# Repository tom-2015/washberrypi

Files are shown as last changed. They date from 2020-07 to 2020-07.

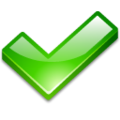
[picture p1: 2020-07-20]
www/ok.png

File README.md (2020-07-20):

# WashberryPi
The main controller board of our washing machine was broken so I decided to do something stupid: create a new controller board with a Raspberry Pi on it!
It turned out not so easy as thought, especially starting centrifuge without having unbalance making the machine to start walking proved a challenge.
After a few months testing and designing new PCB it was finally working again. It's not yet fully completed but if anyone else ever wants to do something this crazy I decided to put everything open source on github.

# Requirements
It's designed for a Samsung co bubble with DC motor but with some adjustments in software and PCB it will probably work with other machines that have a DC motor.
You'll need some skills for PCB design in Eagle, programming Raspberry Pi (Visual Basic .NET) and microcontrollers (Microchip PIC) in C.

# Contens
The repository contains 4 projects:
* Washmachine.sln: the main Visual Studio VB .NET project with software that runs on the Raspberry. This project is the main program of the washing machine. It controls all the components and provides a web interface.
* eagle directory: contains the Eagle files and Gerber files for the PCB that holds the Raspberry Pi Zero W, PIC microcontroller, relays and motor control components.
* pic directory: contains washing_machine.__c which is a Source Boost project containing C-code for the microcontroller that drives the TRIAC for motor.
* www directory: this is the web interface main directory.

# TIPS
Some tips if you want to make your washing machine Raspberry Pi controlled:
* be careful when applying power to the motor, I accidently applied power too fast resulting in a broken bearing! When testing the motor circuit add some resistors in series with the motor.
* If I need to redo the project I would consider using PWM with an IGBT or MOSFET to drive the motor and not using the original Samsung design with a TRIAC. This is because I think it's easier using PWM which in theory could be connected directly to the Pi instead of having a different microcontroller for it.
* Use a Raspberry Pi (2,3,4) with quad core instead of the single core Raspberry Pi Zero W. I needed to use an accelerometer to capture the drum vibrations and this required a thread to read 400 samples a second over I²C. This single core is often interrupted doing other stuff making the accelerometer buffer overflow.

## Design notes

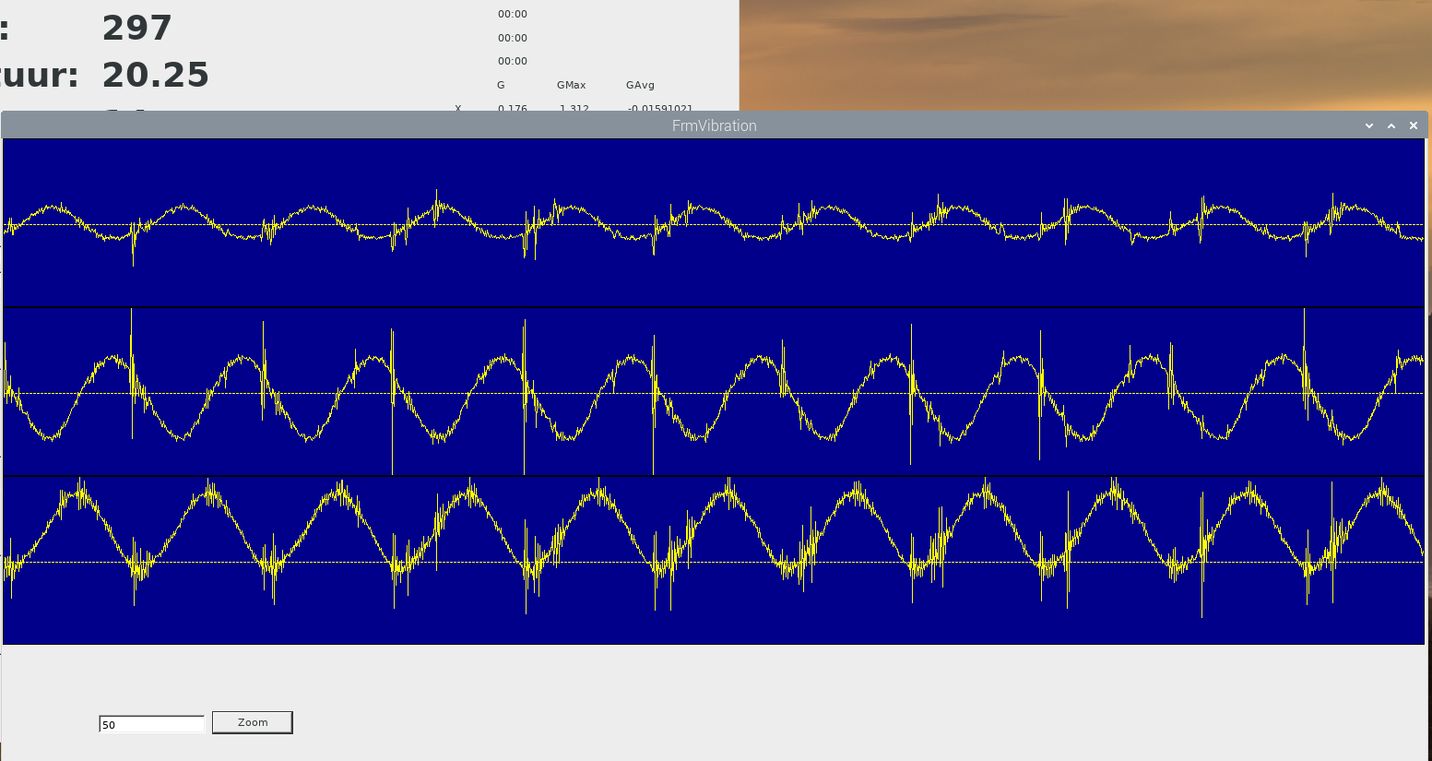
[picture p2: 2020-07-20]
vibration/very_unbalanced.png

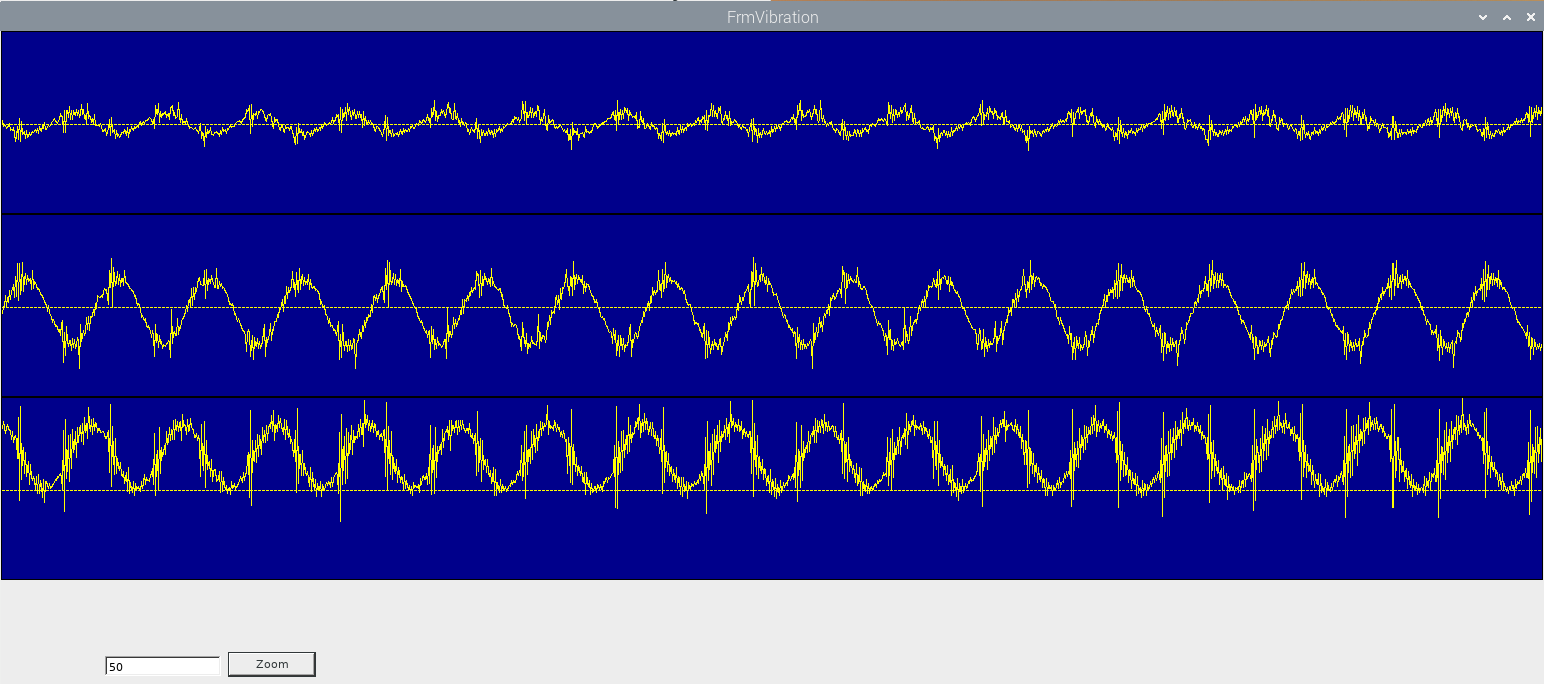
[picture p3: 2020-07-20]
vibration/vibration_450_unbalanced.png

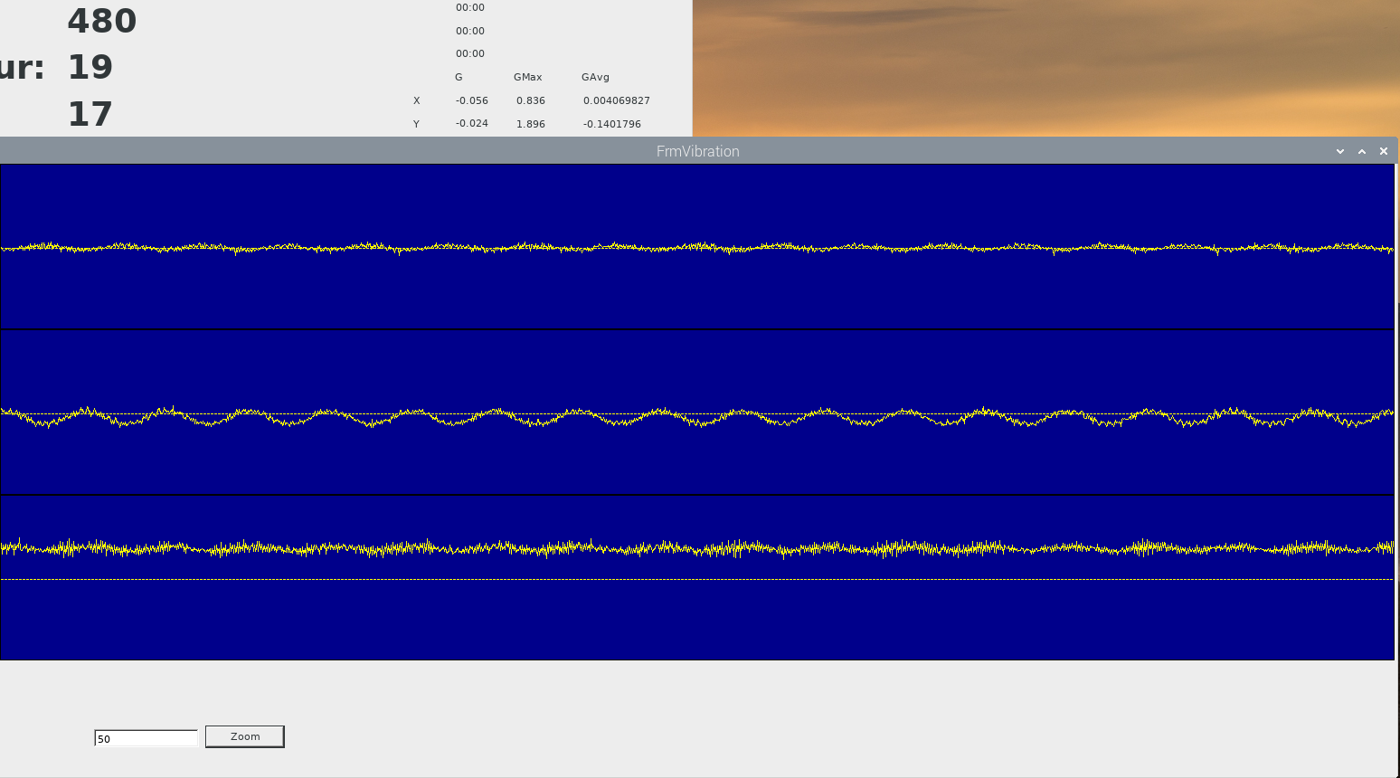
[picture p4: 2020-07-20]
vibration/vibration_450_empty.png

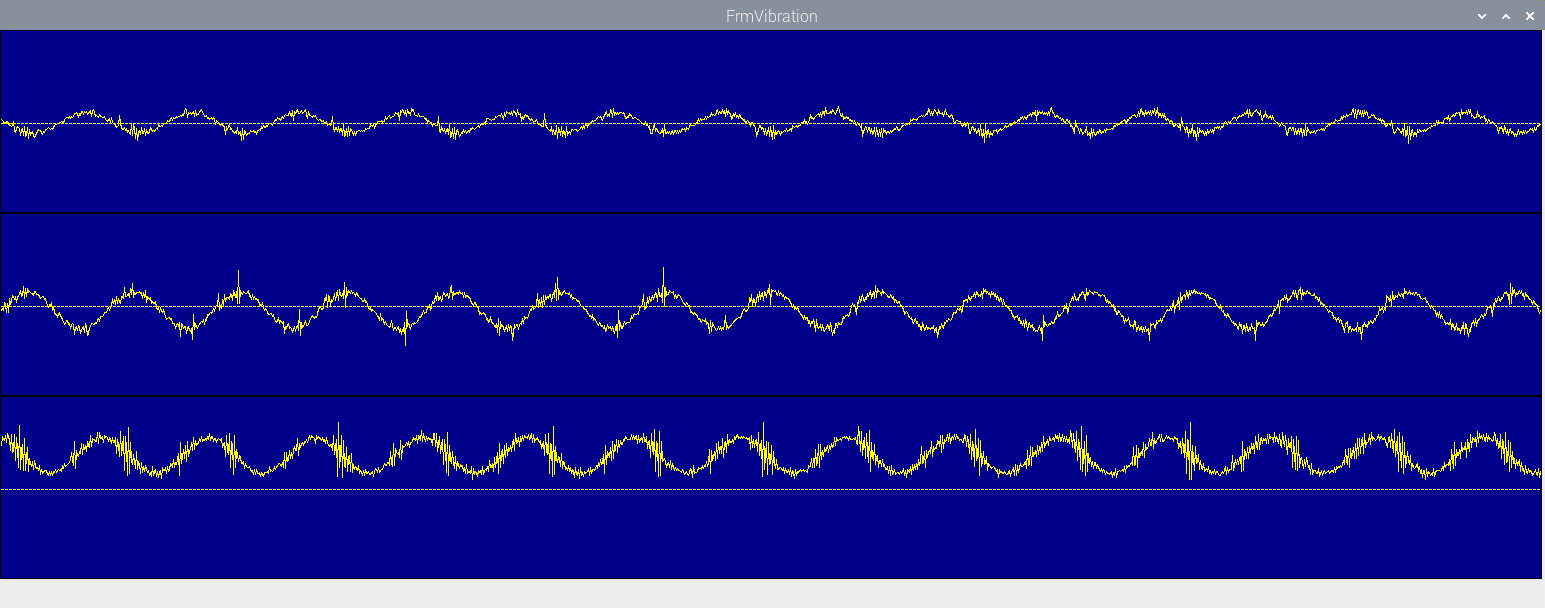
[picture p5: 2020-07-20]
vibration/vibrations.png

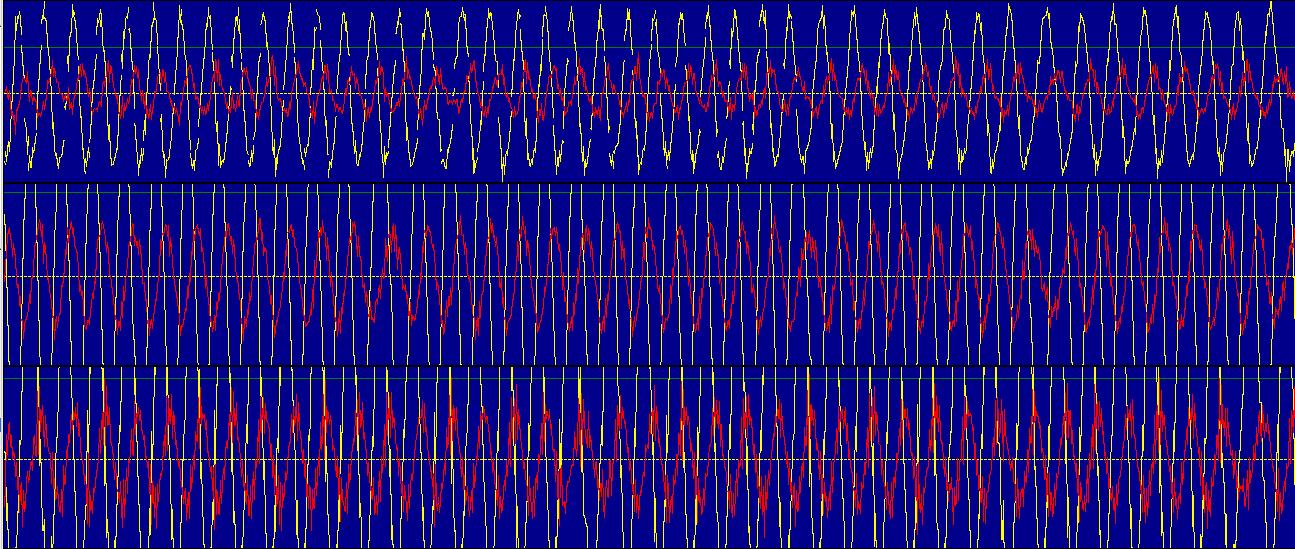
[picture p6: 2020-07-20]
vibration/vibration_high_speed.png

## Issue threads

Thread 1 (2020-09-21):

Washberry PI PCB fabrication

zjobra, 2020-09-21:
Hi!
I've uploaded PCB to pcbhubs - https://pcbhubs.com/newpcb/16007170405f6900f06cf6b#
Do you have a BOM file?

tom-2015, 2020-09-22:
hi,
I did a quick extract from eagle schematic: [https://github.com/tom-2015/washberrypi/blob/master/eagle/washberry-BOM.html](url)
Some parts were reused from the original PCB like the heat sink, input filter capacitors, rectifier, VDR,... So it may be difficult to find a place to buy these.

Maybe you need to redesign the PCB a little to fit components you can find. Most things I bought from https://www.conrad.com/, https://www.farnell.com/ or Aliexpress.

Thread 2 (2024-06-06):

Ideas: Is this project still active, anywhere?

zaqhack, 2024-06-06:
It occurred to me that the basics of washing machine control were fairly universal. A 2-pcb set could likely be created with a universal "motherboard" and a vendor-specific "daughtercard" that could do specific sensor and control protocols. By doing this, the "motherboard" could be refined to provide lots of key features so long as "daughtercard" connected to it would support the feature. In theory, this would allow modes beyond the original manufacturer's settings in some cases.

It also occurs to me that ARM processors, in general, can be direct-mounted on the PCBs in question, which could make for a very cheap alternative to replacing controller boards in some modern washers. Building on what you have done here, it might be possible to have some kind of "Open Washer Project" that ultimately supports a wider variety of hardware.

P.S. https://youtu.be/j-DPf8Oz_9w - for "bouncy washers," this is what you want. (Probably the most-watched thing I'll ever put on YouTube. Yes, that's me.)

tom-2015, 2024-06-11:
The project is not active here anymore, it's available for anyone who wants to make his own controller board.

"Open Washer Project" with universal cards and controller board, yes this would be a cool thing unfortunately I don't have much time to start this 🙈

zaqhack, 2024-06-12:
I'll probably start with a fork of this repository, at some point. Thanks for your response! I'll let you know if I get it off the ground.

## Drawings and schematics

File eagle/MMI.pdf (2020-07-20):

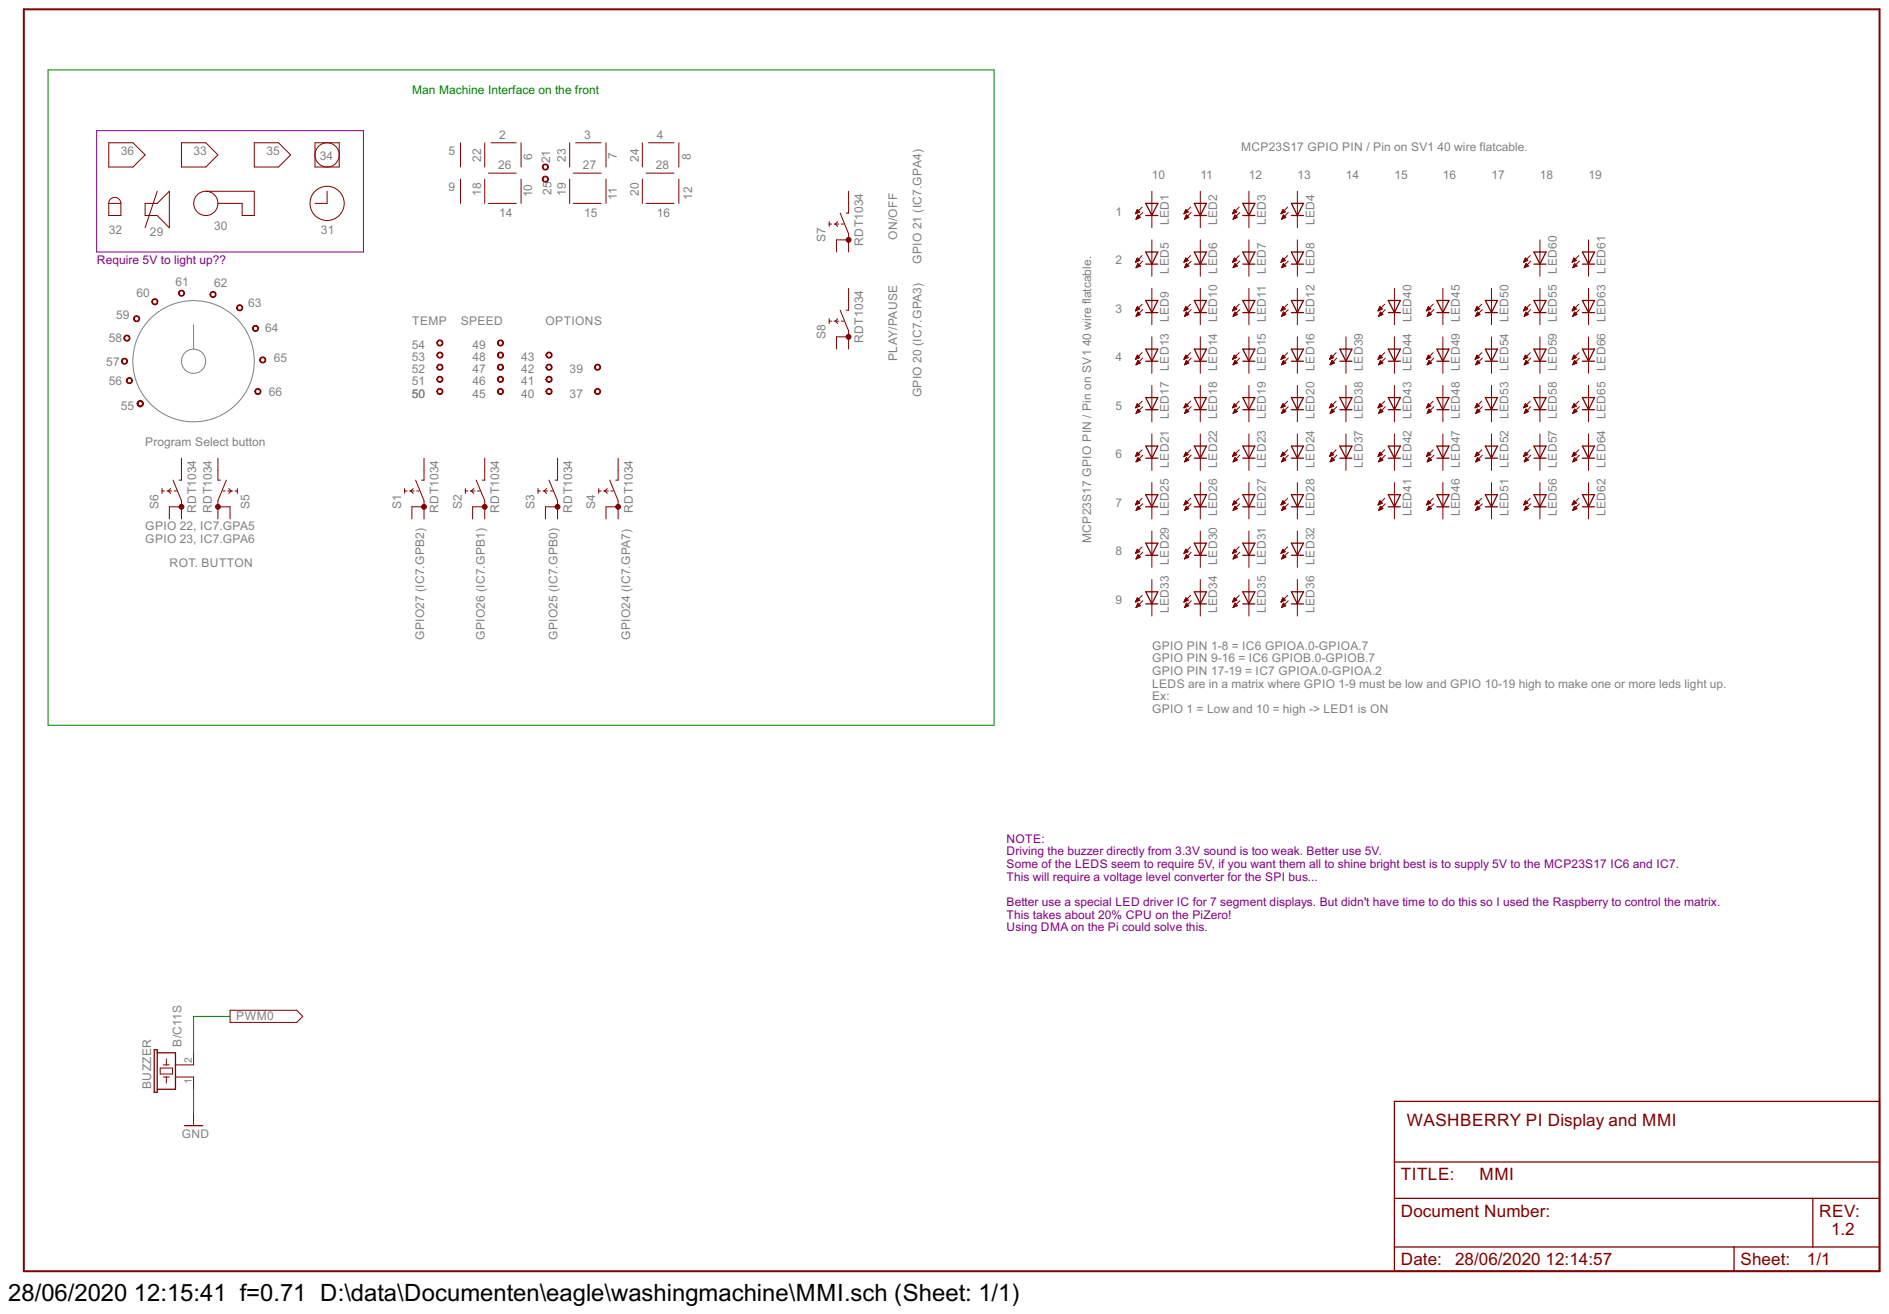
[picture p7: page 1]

Man Machine Interface on the front

MCP23S17 GPIO PIN / Pin on SV1 40 wire flatcable.

ON/OFF PLAY/PAUSE

Require 5V to light up??

GPIO PIN 1-8 = IC6 GPIOA.0-GPIOA.7 GPIO PIN 9-16 = IC6 GPIOB.0-GPIOB.7 GPIO PIN 17-19 = IC7 GPIOA.0-GPIOA.2

LEDS are in a matrix where GPIO 1-9 must be low and GPIO 10-19 high to make one or more leds light up. Ex: GPIO 1 = Low and 10 = high -> LED1 is ON

NOTE: Driving the buzzer directly from 3.3V sound is too weak. Better use 5V. Some of the LEDS seem to require 5V, if you want them all to shine bright best is to supply 5V to the MCP23S17 IC6 and IC7. This will require a voltage level converter for the SPI bus... Better use a special LED driver IC for 7 segment displays. But didn't have time to do this so I used the Raspberry to control the matrix. This takes about 20% CPU on the PiZero! Using DMA on the Pi could solve this.

WASHBERRY PI Display and MMI

REV: TITLE: Document Number: MMI

Date: 28/06/2020 12:14:57 | Sheet: 1/1

28/06/2020 12:15:41 f=0.71 D:\data\Documenten\eagle\washingmachine\MMI.sch (Sheet: 1/1)

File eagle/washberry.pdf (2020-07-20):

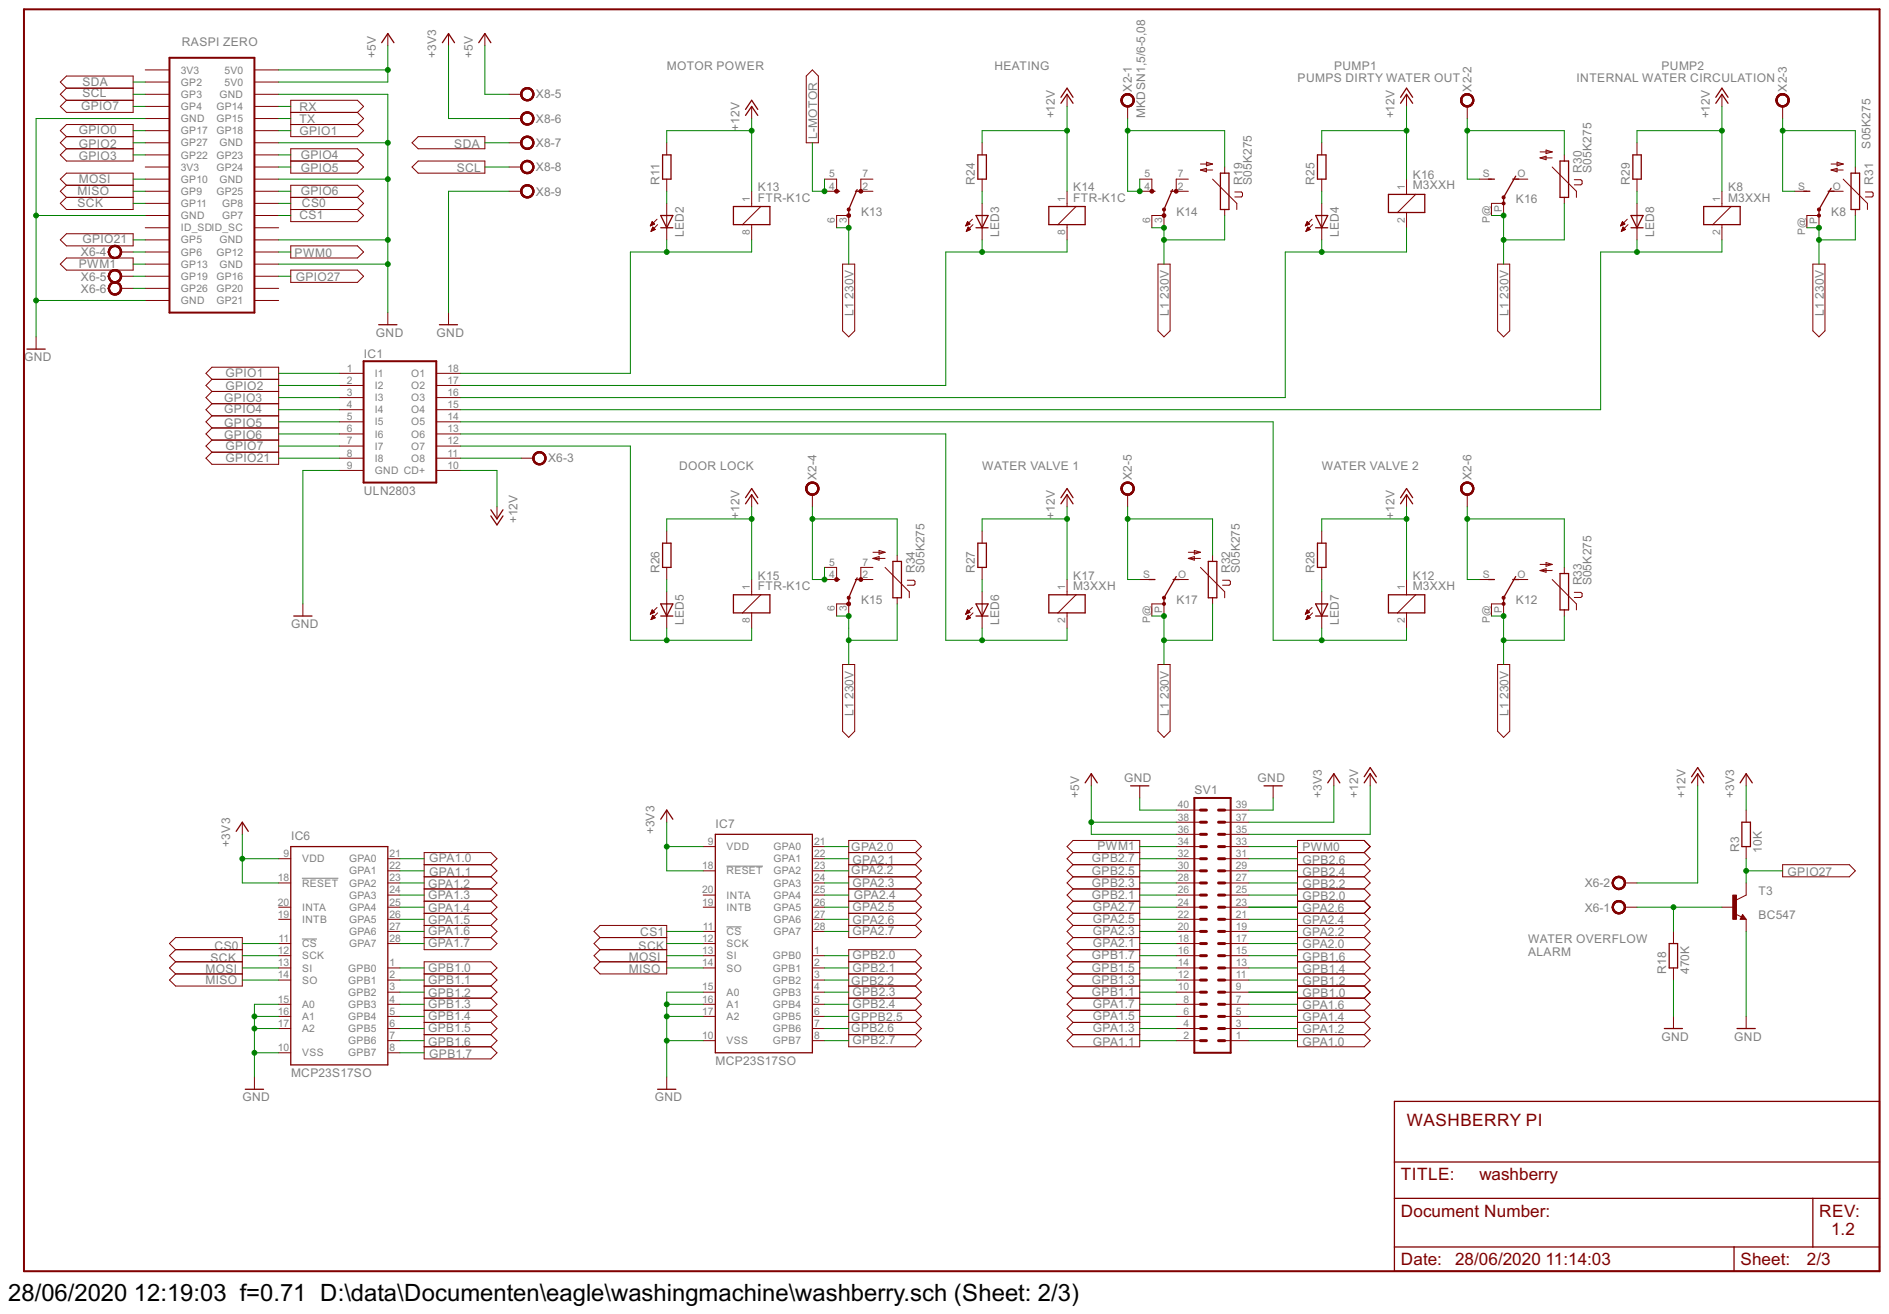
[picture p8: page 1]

2 | 17 O3
3 | 16 O4
4 | 15 O5
6 | 14 O6
7 | 13 O7

REV: TITLE: Document Number: washberry

Date: 28/06/2020 11:14:03 | Sheet: 2/3

28/06/2020 12:19:03 f=0.71 D:\data\Documenten\eagle\washingmachine\washberry.sch (Sheet: 2/3)

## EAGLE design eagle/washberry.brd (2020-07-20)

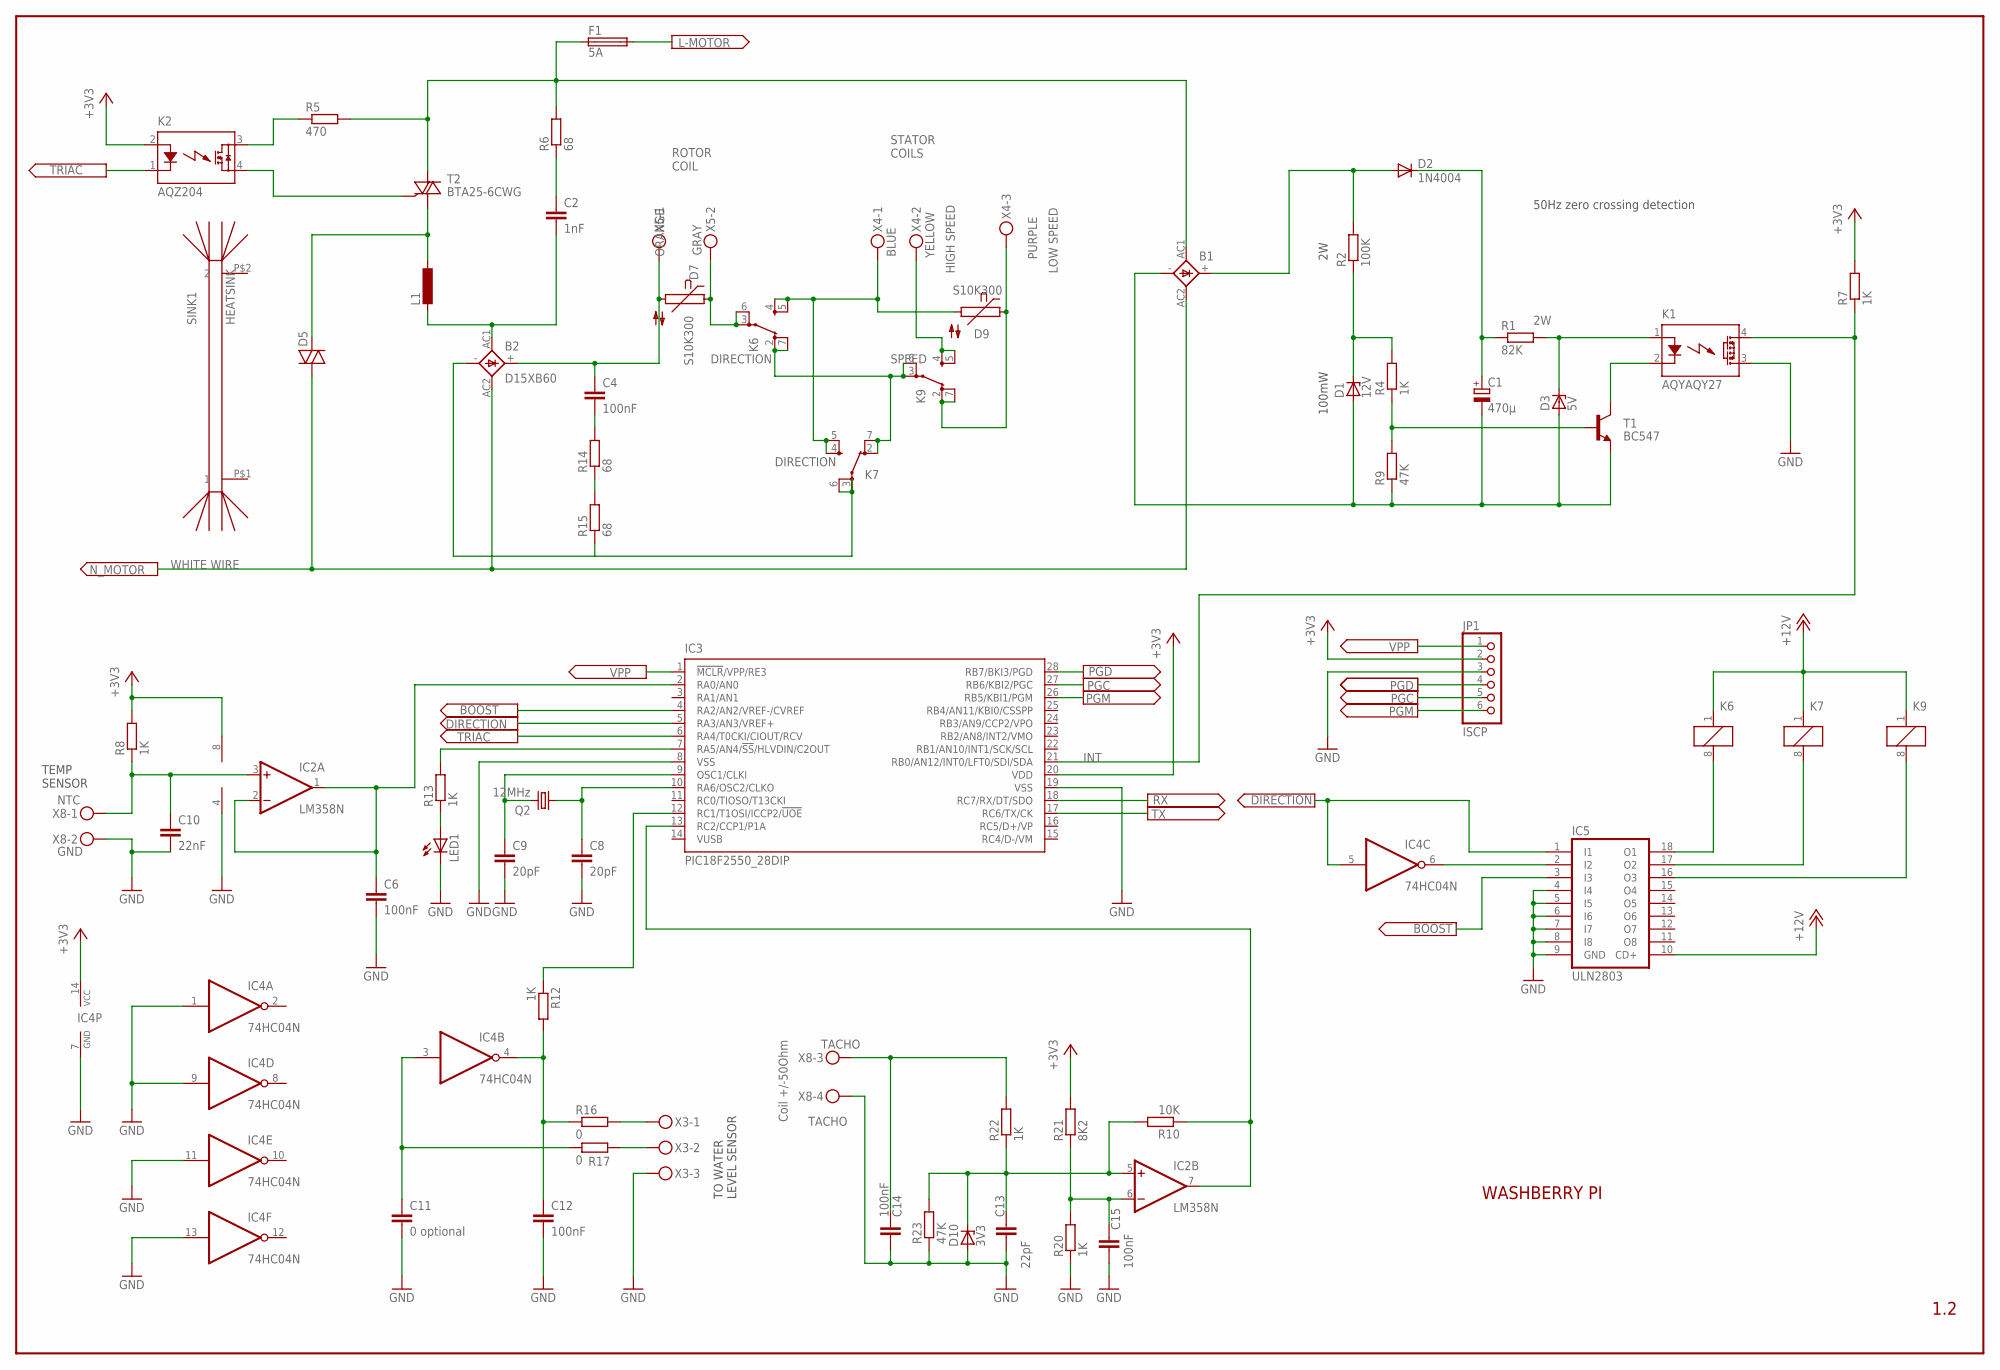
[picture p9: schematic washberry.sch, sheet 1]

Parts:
B1: 2KBB
B2: D15XB60; 5S
C1: 470µ; E5-13
C2: 1nF; C150-054X183
C4: 100nF; C150-054X183
C6, C12, C14, C15: 100nF; C025-024X044
C8, C9: 20pF; C025-024X044
C10: 22nF; C025-024X044
C11: 0 optional; C025-024X044
C13: 22pF; C025-024X044
D1: 12V; DO34Z7
D2: 1N4004; DO41-10
D3: 5V; DO34Z7
D5: DIAC-DO35-10; DO35-10
D7, D9: S10K300
D10: 3V3; DO34Z7
F1: 5A; GSH15
IC2: LM358N; DIL08
IC3: PIC18F2550_28DIP; DIL28-3
IC4: 74HC04N; DIL14
IC5: ULN2803; DIL18
JP1: ISCP; 1X06
K1: AQYAQY27; AQY27
K2: AQZ204; AQZ-SIL04
K6, K7, K9: FTR-K1C
L1: L-EUTJ5-U1; TJ5-U1
LED1: LEDCHIPLED_0805; CHIPLED_0805
Q2: 12MHz; HC49/S
R1: 82K; 0617/17
R2: 100K; 0617/17
R4, R7, R8, R12, R20, R22: 1K; 0411V
R5: 470; P0613/15
R6: 68; P0613/15
R9, R23: 47K; 0411V
R10: 10K; 0411V
R13: 1K; R0805
R14, R15: 68; 0617/17
R16, R17: 0; 0411V
R21: 8K2; 0411V
SINK1: HEATSINK; W_HEATSINK
T1: BC547; TO92
T2: BTA25-6CWG; TO220BV
X3, X4: MKDSN1,5/3-5,08
X5: MKDSN1,5/2-5,08
X8: MKDSN1,5/9-5,08

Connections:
+3V3: IC2.8 (V+), IC3.20 (VDD), IC4.14 (VCC), JP1.2, K2.2 (A), R7.2, R8.2, R21.2; also elsewhere on the board
+12V: IC5.10 (CD+), K6.1, K7.1, K9.1; also elsewhere on the board
BOOST: IC3.4 (RA2/AN2/VREF-/CVREF), IC5.3 (I3)
DIRECTION: IC3.5 (RA3/AN3/VREF+), IC4.5 (I), IC5.1 (I1)
GND: C6.2, C8.2, C9.2, C10.2, C11.2, C12.2, C13.2, C14.2, C15.2, D10.A, IC2.4 (V-), IC3.8 (VSS), IC3.19 (VSS), IC4.1 (I), IC4.7 (GND), IC4.9 (I), IC4.11 (I), IC4.13 (I), IC5.4 (I4), IC5.5 (I5), IC5.6 (I6), IC5.7 (I7), IC5.8 (I8), IC5.9 (GND), JP1.3, K1.3 (DS2), LED1.C, R20.1, R23.1, X3.3, X8.2, X8.4; also elsewhere on the board
INT: IC3.21 (RB0/AN12/INT0/LFT0/SDI/SDA), K1.4 (DS1), R7.1
L-MOTOR: F1.2; also elsewhere on the board
unnamed: K1.2 (K), T1.3 (C)
unnamed: B1.-, C1.-, D1.A, D3.A, R9.1, T1.1 (E)
unnamed: C1.+, D2.C, R1.1
unnamed: D3.C, K1.1 (A), R1.2
unnamed: IC3.7 (RA5/AN4/!SS!/HLVDIN/C2OUT), R13.2
unnamed: LED1.A, R13.1
unnamed: D1.C, R2.1, R4.2
unnamed: R4.1, R9.2, T1.2 (B)
unnamed: B1.+, D2.A, R2.2
unnamed: K2.4 (DS2), T2.G
unnamed: K2.3 (DS1), R5.1
unnamed: IC2.7 (OUT), IC3.13 (RC2/CCP1/P1A), R10.1
unnamed: B2.-, K7.3 (PA), K7.6 (PB), R15.1
unnamed: C2.1, R6.1
unnamed: B2.AC1, C2.2, L1.2
unnamed: C6.1, IC2.1 (OUT), IC2.2 (-IN), IC3.2 (RA0/AN0)
unnamed: K9.4 (SA), K9.5 (SB), X4.2
unnamed: D9.1, K9.2 (OA), K9.7 (OB), X4.3
unnamed: D5.C (2), L1.1, T2.T1 (A1)
unnamed: B2.+, C4.1, D7.2, X5.1
unnamed: C9.1, IC3.9 (OSC1/CLKI), Q2.2
unnamed: C8.1, IC3.10 (RA6/OSC2/CLKO), Q2.1
unnamed: IC3.12 (RC1/T1OSI/ICCP2/!UOE), R12.1
unnamed: C11.1, IC4.3 (I), R17.1
unnamed: C12.1, IC4.4 (O), R12.2, R16.1
unnamed: R14.1, R15.2
unnamed: C4.2, R14.2
unnamed: K6.2 (OA), K6.7 (OB), K7.2 (OA), K7.7 (OB), K9.3 (PA), K9.6 (PB)
unnamed: D9.2, K6.4 (SA), K6.5 (SB), K7.4 (SA), K7.5 (SB), X4.1
unnamed: D7.1, K6.3 (PA), K6.6 (PB), X5.2
unnamed: IC5.18 (O1), K6.8 (2)
unnamed: R16.2, X3.1
unnamed: R17.2, X3.2
unnamed: C15.1, IC2.6 (-IN), R20.2, R21.1
unnamed: C13.1, D10.C, IC2.5 (+IN), R10.2, R22.1, R23.2
unnamed: IC4.6 (O), IC5.2 (I2)
unnamed: IC5.17 (O2), K7.8 (2)
unnamed: IC5.16 (O3), K9.8 (2)
NTC: C10.1, IC2.3 (+IN), R8.1, X8.1
N_MOTOR: B1.AC2, B2.AC2, D5.A (1); also elsewhere on the board
PGC: IC3.27 (RB6/KBI2/PGC), JP1.5
PGD: IC3.28 (RB7/BKI3/PGD), JP1.4
PGM: IC3.26 (RB5/KBI1/PGM), JP1.6
RX: IC3.18 (RC7/RX/DT/SDO); also elsewhere on the board
SUPPLY_MOTOR: B1.AC1, F1.1, R5.2, R6.2, T2.T2 (A2)
TACHO: C14.1, R22.2, X8.3
TRIAC: IC3.6 (RA4/T0CKI/CIOUT/RCV), K2.1 (K)
TX: IC3.17 (RC6/TX/CK); also elsewhere on the board
VPP: IC3.1 (!MCLR!/VPP/RE3), JP1.1

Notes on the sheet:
100mW
TEMP SENSOR
WASHBERRY PI
1.2
ROTOR COIL
STATOR COILS
LOW SPEED
HIGH SPEED
DIRECTION
SPEED
50Hz zero crossing detection
WHITE WIRE
ORANGE
GRAY
BLUE
YELLOW
PURPLE
Coil +/-50Ohm
TO WATER LEVEL SENSOR

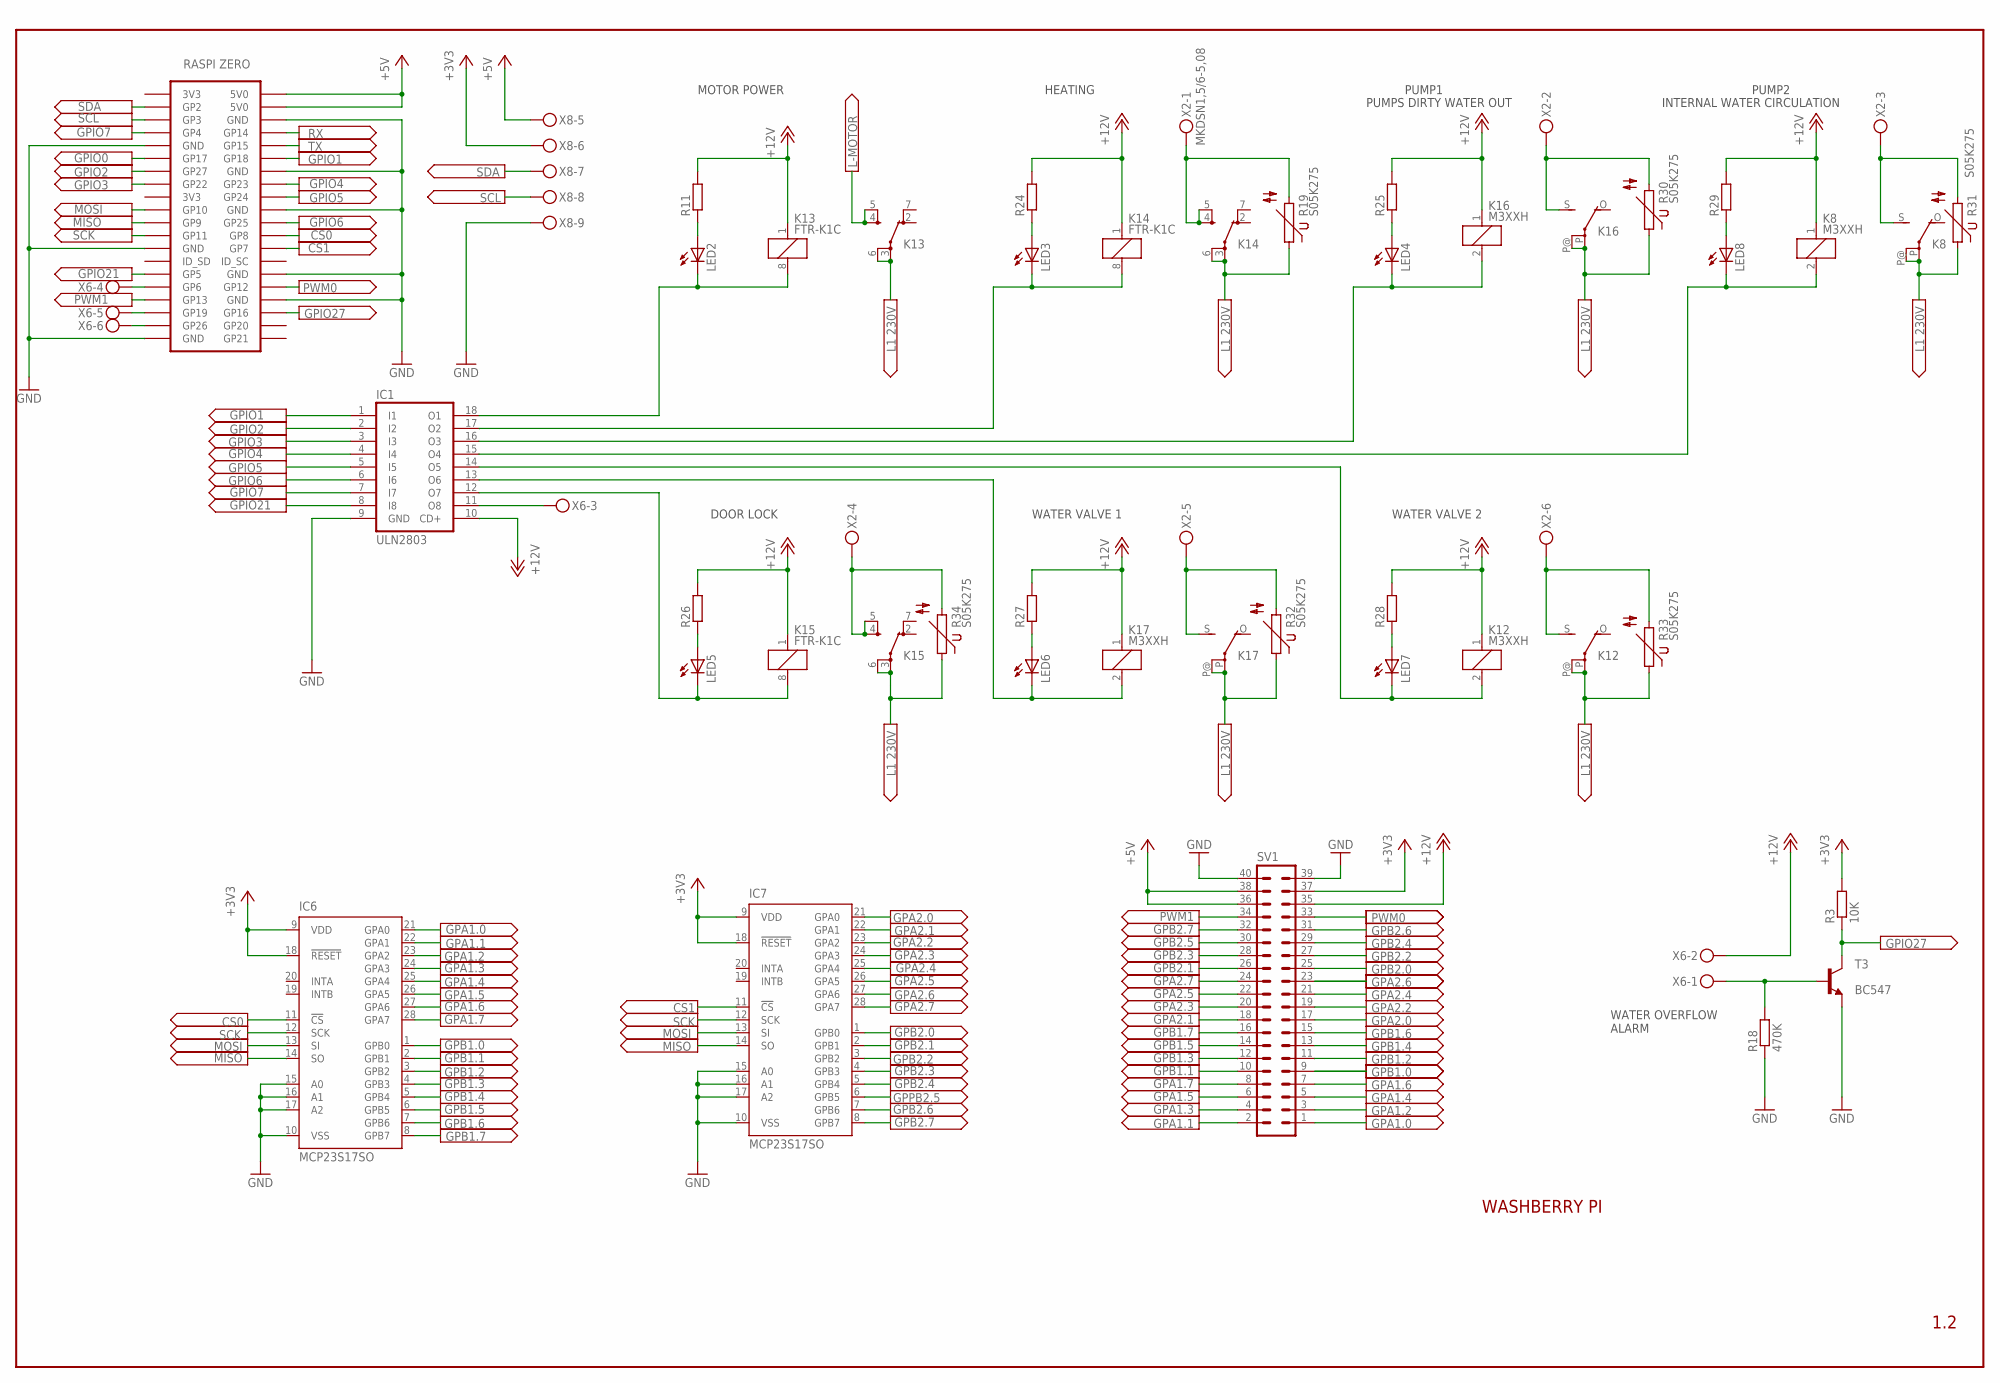
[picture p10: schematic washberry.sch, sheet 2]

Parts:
IC1: ULN2803; DIL18
IC6, IC7: MCP23S17SO; SO28W
K8, K12, K16, K17: M3XXH
K13, K14, K15: FTR-K1C
LED2, LED3, LED4, LED5, LED6, LED7, LED8: LEDSML0805; SML0805
R3: 10K; 0207/2V
R11, R24, R25, R26, R27, R28, R29: R-EU_R0805; R0805
R18: 470K; 0207/2V
R19, R30, R31, R32, R33, R34: S05K275
SV1: ML40
T3: BC547; TO92
U$3: ZERO; ZERO_NO_DIMENSION
X2, X6: MKDSN1,5/6-5,08
X8: MKDSN1,5/9-5,08

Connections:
+3V3: IC6.9 (VDD), IC6.18 (!RESET), IC7.9 (VDD), IC7.18 (!RESET), R3.2, SV1.37, X8.6; also elsewhere on the board
+5V: SV1.36, SV1.38, U$3.2 (5V0), U$3.4 (5V0), X8.5; also elsewhere on the board
+12V: IC1.10 (CD+), K8.1, K12.1, K13.1, K14.1, K15.1, K16.1, K17.1, R11.2, R24.2, R25.2, R26.2, R27.2, R28.2, R29.2, SV1.35, X6.2; also elsewhere on the board
CS0: IC6.11 (!CS), U$3.24 (GP8)
CS1: IC7.11 (!CS), U$3.26 (GP7)
GND: IC1.9 (GND), IC6.10 (VSS), IC6.15 (A0), IC6.16 (A1), IC6.17 (A2), IC7.10 (VSS), IC7.15 (A0), IC7.16 (A1), IC7.17 (A2), R18.1, SV1.39, SV1.40, T3.1 (E), U$3.6 (GND), U$3.9 (GND), U$3.14 (GND), U$3.20 (GND), U$3.25 (GND), U$3.30 (GND), U$3.34 (GND), U$3.39 (GND), X8.9; also elsewhere on the board
GPA1.0: IC6.21 (GPA0), SV1.1
GPA1.1: IC6.22 (GPA1), SV1.2
GPA1.2: IC6.23 (GPA2), SV1.3
GPA1.3: IC6.24 (GPA3), SV1.4
GPA1.4: IC6.25 (GPA4), SV1.5
GPA1.5: IC6.26 (GPA5), SV1.6
GPA1.6: IC6.27 (GPA6), SV1.7
GPA1.7: IC6.28 (GPA7), SV1.8
GPA2.0: IC7.21 (GPA0), SV1.17
GPA2.1: IC7.22 (GPA1), SV1.18
GPA2.2: IC7.23 (GPA2), SV1.19
GPA2.3: IC7.24 (GPA3), SV1.20
GPA2.4: IC7.25 (GPA4), SV1.21
GPA2.5: IC7.26 (GPA5), SV1.22
GPA2.6: IC7.27 (GPA6), SV1.23
GPA2.7: IC7.28 (GPA7), SV1.24
GPB1.0: IC6.1 (GPB0), SV1.9
GPB1.1: IC6.2 (GPB1), SV1.10
GPB1.2: IC6.3 (GPB2), SV1.11
GPB1.3: IC6.4 (GPB3), SV1.12
GPB1.4: IC6.5 (GPB4), SV1.13
GPB1.5: IC6.6 (GPB5), SV1.14
GPB1.6: IC6.7 (GPB6), SV1.15
GPB1.7: IC6.8 (GPB7), SV1.16
GPB2.0: IC7.1 (GPB0), SV1.25
GPB2.1: IC7.2 (GPB1), SV1.26
GPB2.2: IC7.3 (GPB2), SV1.27
GPB2.3: IC7.4 (GPB3), SV1.28
GPB2.4: IC7.5 (GPB4), SV1.29
GPB2.5: SV1.30
GPB2.6: IC7.7 (GPB6), SV1.31
GPB2.7: IC7.8 (GPB7), SV1.32
GPIO0: U$3.11 (GP17)
GPIO1: IC1.1 (I1), U$3.12 (GP18)
GPIO2: IC1.2 (I2), U$3.13 (GP27)
GPIO3: IC1.3 (I3), U$3.15 (GP22)
GPIO4: IC1.4 (I4), U$3.16 (GP23)
GPIO5: IC1.5 (I5), U$3.18 (GP24)
GPIO6: IC1.6 (I6), U$3.22 (GP25)
GPIO7: IC1.7 (I7), U$3.7 (GP4)
GPIO21: IC1.8 (I8), U$3.29 (GP5)
GPIO27: R3.1, T3.3 (C), U$3.36 (GP16)
GPPB2.5: IC7.6 (GPB5)
L: K8.P, K8.P@, K12.P, K12.P@, K13.3 (PA), K13.6 (PB), K14.3 (PA), K14.6 (PB), K15.3 (PA), K15.6 (PB), K16.P, K16.P@, K17.P, K17.P@, R19.1, R30.1, R31.1, R32.1, R33.1, R34.1; also elsewhere on the board
L-MOTOR: K13.4 (SA), K13.5 (SB); also elsewhere on the board
MISO: IC6.14 (SO), IC7.14 (SO), U$3.21 (GP9)
MOSI: IC6.13 (SI), IC7.13 (SI), U$3.19 (GP10)
unnamed: IC1.11 (O8), X6.3
unnamed: R18.2, T3.2 (B), X6.1
unnamed: IC1.18 (O1), K13.8 (2), LED2.C
unnamed: LED2.A, R11.1
unnamed: IC1.17 (O2), K14.8 (2), LED3.C
unnamed: LED3.A, R24.1
unnamed: IC1.16 (O3), K16.2, LED4.C
unnamed: U$3.31 (GP6), X6.4
unnamed: U$3.35 (GP19), X6.5
unnamed: LED4.A, R25.1
unnamed: LED5.A, R26.1
unnamed: IC1.13 (O6), K17.2, LED6.C
unnamed: LED6.A, R27.1
unnamed: IC1.14 (O5), K12.2, LED7.C
unnamed: LED7.A, R28.1
unnamed: IC1.15 (O4), K8.2, LED8.C
unnamed: LED8.A, R29.1
unnamed: IC1.12 (O7), K15.8 (2), LED5.C
unnamed: U$3.37 (GP26), X6.6
unnamed: K14.4 (SA), K14.5 (SB), R19.2, X2.1
unnamed: K16.S, R30.2, X2.2
unnamed: K8.S, R31.2, X2.3
unnamed: K12.S, R33.2, X2.6
unnamed: K17.S, R32.2, X2.5
unnamed: K15.4 (SA), K15.5 (SB), R34.2, X2.4
PWM0: SV1.33, U$3.32 (GP12)
PWM1: SV1.34, U$3.33 (GP13)
RX: U$3.8 (GP14); also elsewhere on the board
SCK: IC6.12 (SCK), IC7.12 (SCK), U$3.23 (GP11)
SCL: U$3.5 (GP3), X8.8
SDA: U$3.3 (GP2), X8.7
TX: U$3.10 (GP15); also elsewhere on the board

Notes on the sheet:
WASHBERRY PI
1.2
MOTOR POWER
HEATING
PUMP1
PUMP2
DOOR LOCK
WATER VALVE 1
WATER VALVE 2
PUMPS DIRTY WATER OUT
INTERNAL WATER CIRCULATION
WATER OVERFLOW ALARM

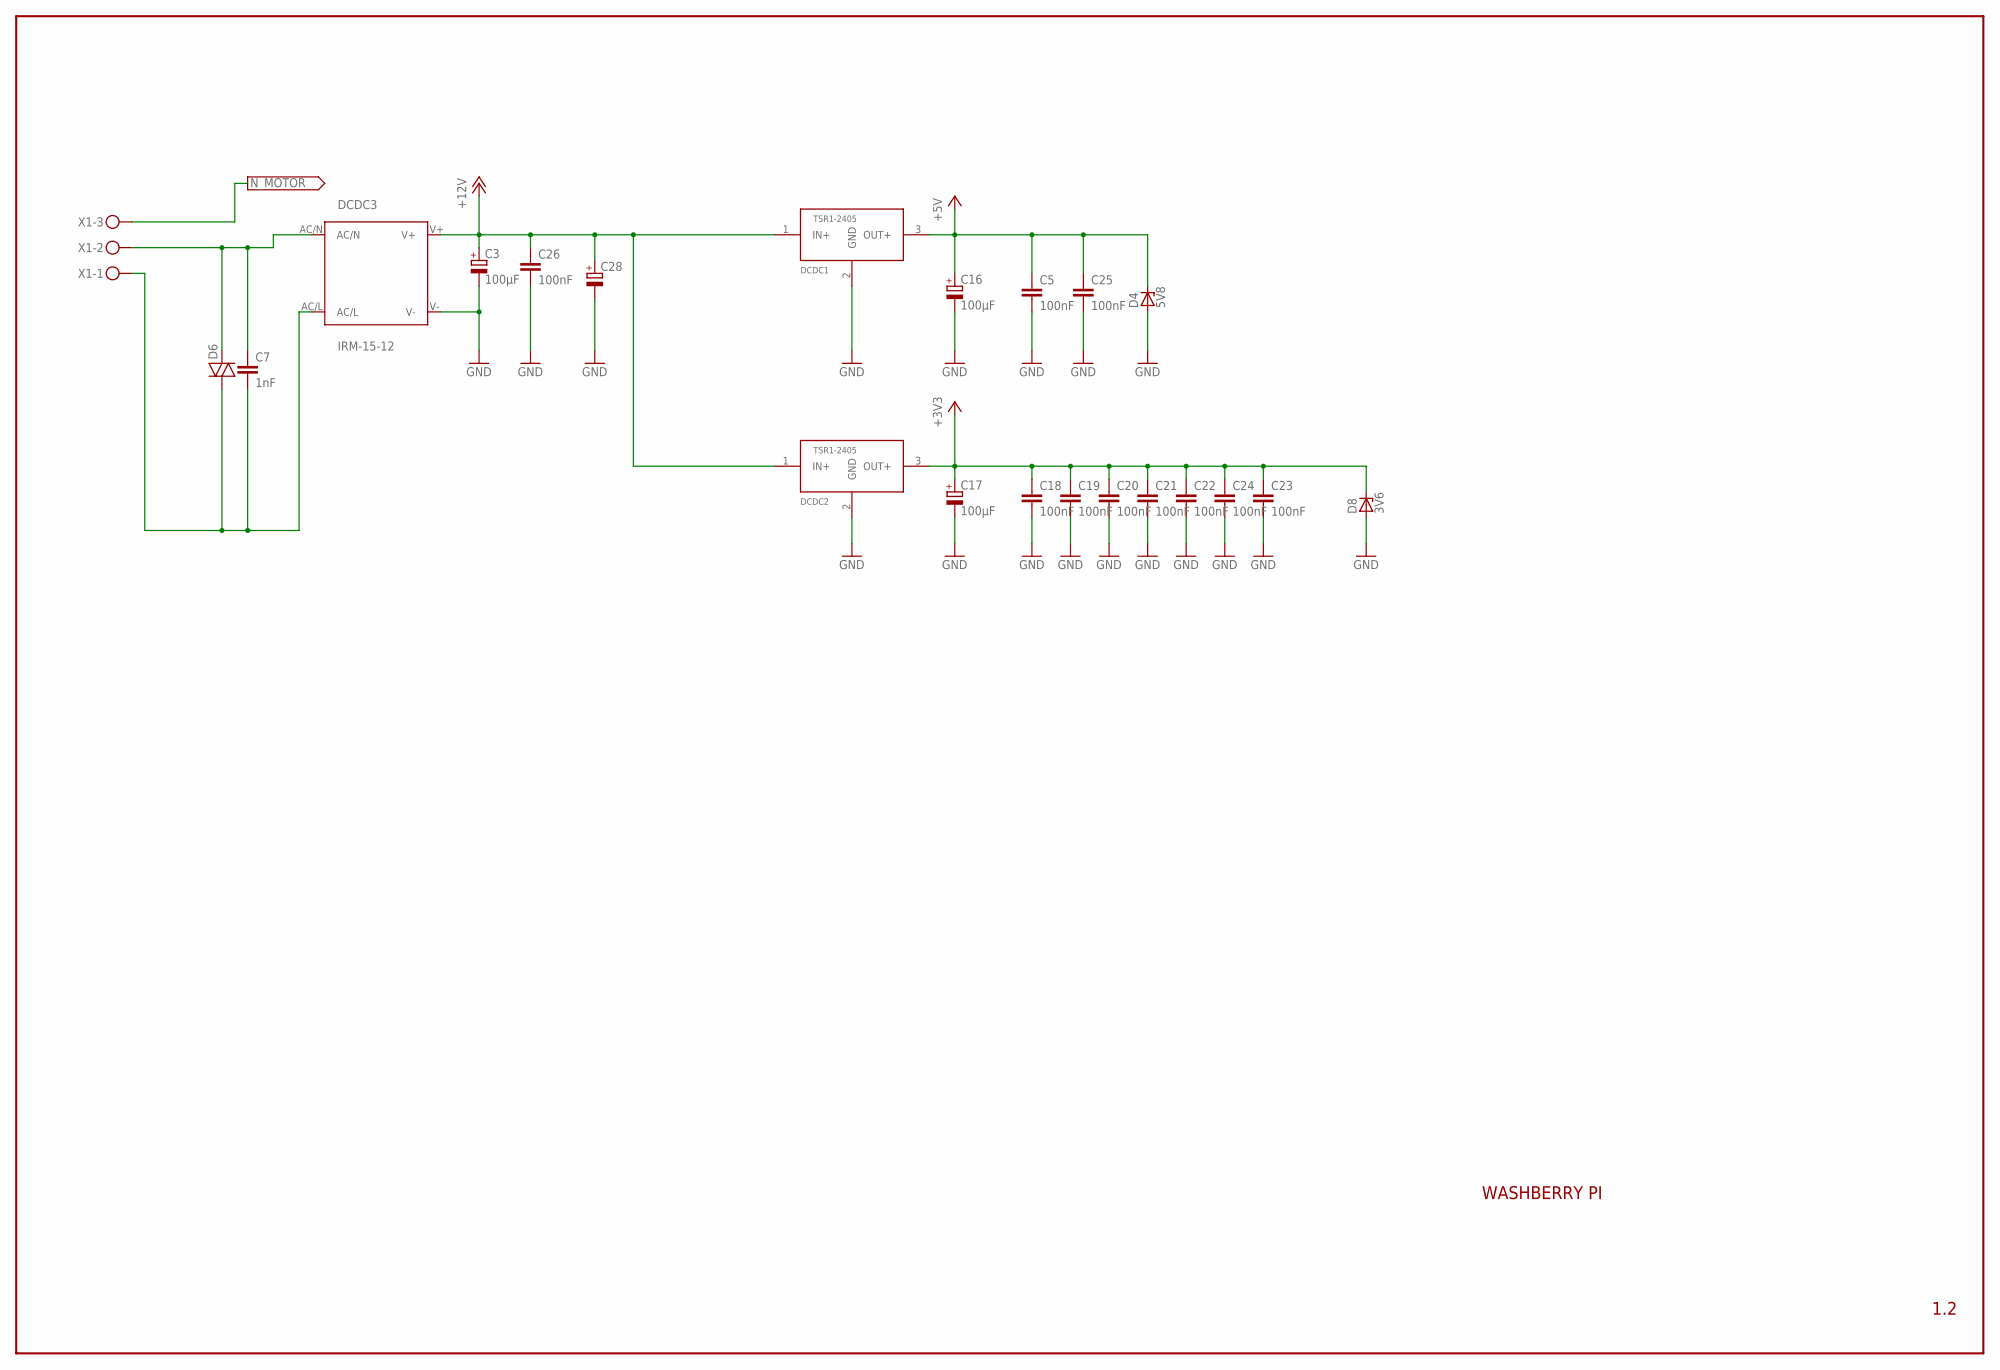
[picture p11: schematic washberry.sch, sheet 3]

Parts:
C3, C16: 100µF; E3,5-8
C5, C18, C19, C20, C21, C22, C23, C24, C25, C26: 100nF; C025-024X044
C7: 1nF; C150-091X182
C17: 100µF; E2-5
C28: CPOL-EUE2-5; E2-5
D4: 5V8; DO34Z7
D6: DIAC-DO35-10; DO35-10
D8: 3V6; DO34Z7
DCDC1, DCDC2: TSR1-2405; SIPTO220
DCDC3: IRM-15-12; IRM_15/20
X1: MKDSN1,5/3-5,08

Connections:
+3V3: C17.+, C18.1, C19.1, C20.1, C21.1, C22.1, C23.1, C24.1, D8.C, DCDC2.3 (OUT+); also elsewhere on the board
+5V: C5.1, C16.+, C25.1, D4.C, DCDC1.3 (OUT+); also elsewhere on the board
+12V: C3.+, C26.1, C28.+, DCDC1.1 (IN+), DCDC2.1 (IN+), DCDC3.V+; also elsewhere on the board
GND: C3.-, C5.2, C16.-, C17.-, C18.2, C19.2, C20.2, C21.2, C22.2, C23.2, C24.2, C25.2, C26.2, C28.-, D4.A, D8.A, DCDC1.2 (GND), DCDC2.2 (GND), DCDC3.V-; also elsewhere on the board
L: C7.2, D6.A (1), DCDC3.AC/L, X1.1; also elsewhere on the board
N: C7.1, D6.C (2), DCDC3.AC/N, X1.2
N_MOTOR: X1.3; also elsewhere on the board

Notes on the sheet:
WASHBERRY PI
1.2

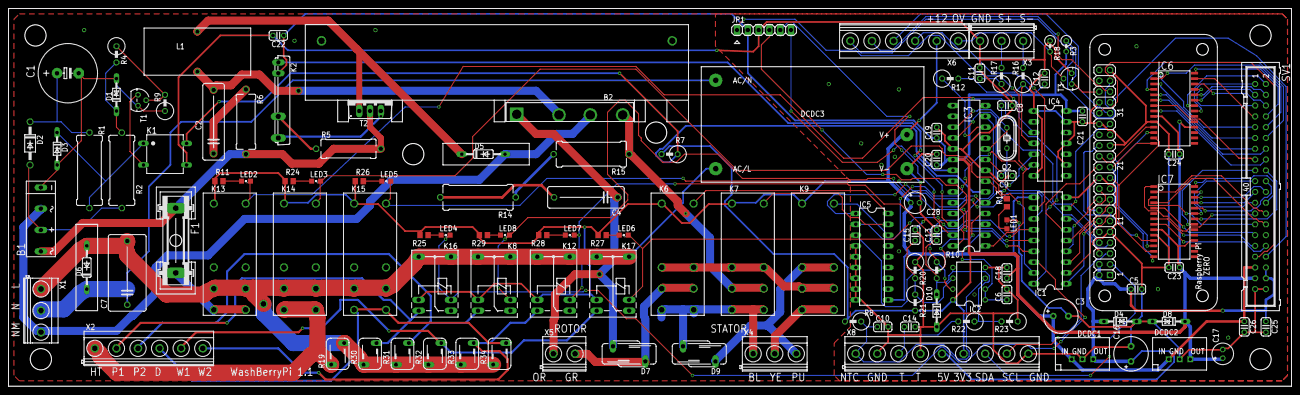
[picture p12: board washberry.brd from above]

Board: 2 copper layers, 301.9 x 88.9 mm, 120 parts (0 on the bottom side), 133 nets.

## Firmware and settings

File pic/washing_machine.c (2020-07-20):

#include <system.h>
#include <system.h>
#include <stdio.h>
#include <string.h>
#include <stdlib.h>
#include <memory.h>
#include "sp.h"

#pragma CLOCK_FREQ 48000000

//#pragma DATA	_CONFIG1L, _PLLDIV_5_1L & _CPUDIV_OSC1_PLL2_1L & _USBDIV_2_1L  //20Mhz
#pragma DATA	_CONFIG1L, _PLLDIV_3_1L & _CPUDIV_OSC1_PLL2_1L & _USBDIV_2_1L  //12Mhz
#pragma DATA    _CONFIG1H, _FOSC_HSPLL_HS_1H & _FCMEN_OFF_1H & _IESO_OFF_1H

//#pragma DATA    _CONFIG2L, _PWRT_OFF_2L & _BOR_OFF_2L  & _VREGEN_ON_2L
#pragma DATA    _CONFIG2L, _PWRT_OFF_2L & _BOR_ON_2L & _BORV_3_2L  & _VREGEN_ON_2L
#pragma DATA    _CONFIG2H, _WDT_ON_2H & _WDTPS_64_2H // 1/4 sec, _WDTPS_1024_2H //WDT ON, 4s
#pragma DATA    _CONFIG3H, _CCP2MX_ON_3H & _LPT1OSC_OFF_3H & _PBADEN_OFF_3H & _MCLRE_OFF_3H
#pragma DATA    _CONFIG4L, _STVREN_ON_4L & _LVP_OFF_4L & _DEBUG_OFF_4L & _XINST_OFF_4L
#pragma DATA    _CONFIG5L, _CP0_OFF_5L & _CP1_OFF_5L & _CP2_OFF_5L & _CP3_OFF_5L
#pragma DATA    _CONFIG5H, _CPB_OFF_5H & _CPD_OFF_5H
#pragma DATA    _CONFIG6L, _WRT0_OFF_6L & _WRT1_OFF_6L & _WRT2_OFF_6L & _WRT3_OFF_6L
#pragma DATA    _CONFIG6H, _WRTC_OFF_6H & _WRTB_OFF_6H & _WRTD_OFF_6H
#pragma DATA    _CONFIG7L, _EBTR0_OFF_7L & _EBTR1_OFF_7L & _EBTR2_OFF_7L & _EBTR3_OFF_7L
#pragma DATA    _CONFIG7H, _EBTRB_OFF_7H


#define TRIAC_ON 0
#define TRIAC_OFF 1
#define TRIAC_OUTPUT porta.4
#define DIRECTION_OUTPUT porta.3
#define BOOST_OUTPUT porta.2
#define LED_OUTPUT porta.5

//error bits in error byte
#define ERROR_ZERO_CROSSING 1
#define ERROR_TACHO 2
#define ERROR_WATER 3
#define ERROR_SUNBALANCE 4
#define ERROR_DUNBALANCE 5

//#define TRIAC_OUTPUT porta.3

int wanted_speed=0;
unsigned int current_speed=0;
bool direction=0;          //0 -> speed +, 1 -> speed -
bool changing_direction=0; //becomes 1 if we need to change direction (wait for 0 rpm)
bool speed_control_enabled=true;

unsigned int temperature=0; //holds result of ADC
bool adc_started; //1 if an ADC was started previously

unsigned int tacho_time=0; //time measured between 16 pulses, 1 timer tick is 8µs, drum speed is: +/- 10 ms / (timer / 16 * 0.008)
unsigned int tacho_min=0xFFFF;
unsigned int tacho_max=0;
unsigned char captures=0;
unsigned int p_tacho_min=0;
unsigned int p_tacho_max=0;
bool tacho_captured=false;
unsigned int water_level=0; //time measured of water level frequency
unsigned int water_level_min=0xFFFF;
unsigned int water_level_max=0;
unsigned int p_water_level_min=0;
unsigned int p_water_level_max=0;
unsigned char water_level_captures=0;
bool water_level_captured=false;

unsigned char output_power=0; //holds value of wanted power 0-100% will be converted to triac_on period value
unsigned char rx_buff[32];    //holds received serial data
unsigned char rx_idx=0;       //position of last character
bool serial_cmd_received=0;

unsigned char triac_on=255; //when must triac be turned on in 0.2 ms, 0 = immediately, value range 0-49, triac will be max of 0.2ms on
unsigned char triac_off=255;
unsigned char period_timer=0; //timer that increases every 0.2 ms

unsigned char next_triac_on=255; //buffer of values to be copied to triac_on and triac_off on next sine wave start
unsigned char next_triac_off=255;

unsigned int clock=0; //increments every +/- 10 ms

unsigned char error=0;

void interrupt(){
	if (intcon.INT0F){
		//zero crossing detected
		//fill timer 2 register
		tmr2=0;			
		pir1.TMR2IF=0;
		period_timer=0; //50Hz starts now, sync the timer
		triac_on=next_triac_on;
		triac_off=next_triac_off;
		TRIAC_OUTPUT=TRIAC_OFF;
		intcon.INT0F=0;
	}
	
	if (pir1.TMR2IF){ //interrupt every 0.2ms / 5KHz
		if (period_timer!=255){ //invalid value, no zero crossing detected
			if (period_timer == triac_on){ //see if we must turn on the triac
				TRIAC_OUTPUT = TRIAC_ON;
			}else if (period_timer >= triac_off){ //must turn off triac?
				TRIAC_OUTPUT = TRIAC_OFF;
			}
			error.ERROR_ZERO_CROSSING=0;
			period_timer++; //hold period timer (this is time within half a sine)			
		}else{
			error.ERROR_ZERO_CROSSING=1;
			TRIAC_OUTPUT = TRIAC_OFF;
		}

		pir1.TMR2IF=0;
	}

	//if timer 1 overflows motor is not turning
	if (pir1.TMR1IF){
		tacho_time=0;
		pir1.TMR1IF=0;
		tacho_captured=true;
		if (triac_on!=255) error.ERROR_TACHO=1; //set error if motor should be running
	}
	
	//this captures/measures the frequency of the tacho
	if (pir1.CCP1IF){
		t1con.TMR1ON=0;
		tacho_captured=true;
		MAKESHORT(tacho_time, ccpr1l, ccpr1h);
		tmr1h=0;
		tmr1l=0;
		t1con.TMR1ON=1;
		pir1.CCP1IF=0;
		error.ERROR_TACHO=0;
	}
	
	if (pir2.CCP2IF){
		t3con.TMR3ON=0;
		water_level_captured=true;
		MAKESHORT(water_level, ccpr2l, ccpr2h);
		tmr3h=0;
		tmr3l=0;
		error.ERROR_WATER=0;
		t3con.TMR3ON=1;
		pir2.CCP2IF=0;	
	}

}

//low priority interrupts
void interrupt_low(){

	if (intcon.TMR0IF){
		clock++;
		intcon.TMR0IF=0;
	}

	//serial receive interrupt
	if (pir1.RCIF){ 
		unsigned char rx = rcreg;
		LED_OUTPUT = ~ LED_OUTPUT;
		if (rx!='\r'){
			if (rx=='\n'){
				serial_cmd_received=1;
				rx=0;
			}
			rx_buff[rx_idx] = rx;
			rx_idx++;
			if (rx_idx==sizeof(rx_buff)) rx_idx=0;
		}
	}
	

	
	//error TMR3 is not supposed to flow over
	if (pir2.TMR3IF){
		water_level_captured=true;
		water_level=0;
		pir2.TMR3IF=0;
		error.ERROR_WATER=1;
	}

}

void set_power(unsigned int val){
	if (val > output_power){
		if (output_power ==0){
			if (val > 30) val = 30;
		}else{
			if ((val - output_power) > 10){ //for safety reason, you don't want motor to go from 0 to 100% power in 1 step because of a bug
				val = output_power + 10;
			}
		}
	}
	
	//if no power to motor do not increase power
	if (error.ERROR_ZERO_CROSSING){
		output_power=0;
		return;
	}
	
	output_power = val;

	unsigned char center = 100-output_power;
	if (center < 95){
		if (center<3){
			next_triac_on=0;
			next_triac_off=255;
		}else{
			next_triac_off=center+3;
			next_triac_on=center-3;
		}
	}else{
		next_triac_off=255;
		next_triac_on=255;
	}

}


unsigned int get_water_level_min(){
	water_level_captured=false;
	unsigned int water_level_min_cpy = p_water_level_min;
	if (water_level_captured) water_level_min_cpy = p_water_level_min;
	return water_level_min_cpy;
}

unsigned int get_water_level_max(){
	water_level_captured=false;
	unsigned int water_level_max_cpy = p_water_level_max;
	if (water_level_captured) water_level_max_cpy = p_water_level_max;
	return water_level_max_cpy;
}

unsigned int get_tacho_min(){
	tacho_captured=false;
	unsigned int tacho_min_cpy = p_tacho_min;
	if (tacho_captured) tacho_min_cpy = p_tacho_min;
	return tacho_min_cpy;
}

unsigned int get_tacho_max(){
	tacho_captured=false;
	unsigned int tacho_max_cpy = p_tacho_max;
	if (tacho_captured) tacho_max_cpy = p_tacho_max;
	return tacho_max_cpy;
}

//returns tacho time
unsigned int get_tacho_time(){
	tacho_captured=false;
	unsigned int tacho_time_cpy = tacho_time;
	if (tacho_captured) tacho_time_cpy = tacho_time;
	return tacho_time_cpy;
}

unsigned int get_water_level(){
	water_level_captured=false;
	unsigned int water_level_cpy = water_level;
	if (water_level_captured) water_level_cpy=water_level;
	return water_level_cpy;
}

unsigned int get_rpm(){
	//  (10000/ tacho_time/16*8)*60 -> 60000 / (tacho_time / 2)
	//return ((unsigned int)((unsigned long)639559 / (unsigned long)(tacho_time))) << 1;
	
	//tacho_time * 2 / 3 --> time in µS --> 10 000 / (tacho_time * 2 / 3) *60 --> 15 000 / tacho_time *60
	unsigned long tacho_time_cpy=get_tacho_time();
	if (tacho_time_cpy==0) return 0;
	return (unsigned int) ((unsigned long)900000 / tacho_time_cpy);
	
	
}


unsigned char power_adjust_delay=2;
unsigned char power_adjust_idx=0;

//adjusts power to match wanted speed
void adjust_power(){
	unsigned int wanted;
	
	if (!speed_control_enabled) return; //exit if auto speed control is disabled
	
	if (direction){
		wanted = -wanted_speed;
	}else{
		wanted = wanted_speed;
	}
	
	unsigned int upper = wanted + wanted  / 15;
	unsigned int lower = wanted - wanted  / 15;
	
	current_speed = get_rpm();
	
	if (wanted>=60){
		power_adjust_delay=2;
	}else{
		if (current_speed<20){
			power_adjust_delay=2;
		}else if (current_speed < 20){
			power_adjust_delay=10;
		}else if (current_speed < 30){
			power_adjust_delay=18;
		}else if (current_speed < 50){
			power_adjust_delay=30;
		}else{
			power_adjust_delay=60;
		}
	}
	

	if (changing_direction){
		if (current_speed<10){
			changing_direction=0;
			DIRECTION_OUTPUT=direction;
			set_power(0);
		}	
	}else{
		if (wanted == 0){
			set_power(0);
		}else if (current_speed < lower){
			if (output_power<20){
				set_power(25);
			}
			if (output_power<100){
				if (output_power > 45 && current_speed < 5) output_power = 45; //saftey prevent power going up if no voltage goes to motor
				if (power_adjust_idx>=power_adjust_delay || output_power < 25){
					set_power(output_power+1);
					power_adjust_idx=0;
				}
				power_adjust_idx++;
			}
		}else if (current_speed > upper){
			if (output_power<10) output_power=0;
			if (output_power>0){
				set_power(output_power-1);
			}
		}
	}

}

void set_wanted_speed(int rpm){
	if (rpm==0){
		set_power(0);
	}else if (rpm < 0){
		if (direction==0){
			direction=1;
			changing_direction=1;
			set_power(0);
		}
	}else{
		if (direction==1){
			direction=0;
			changing_direction=1;
			set_power(0);
		}
	}
	wanted_speed=rpm;
}

void read_temperature(){
	if(adcon0.GO_DONE==0){
		if(adc_started){
			MAKESHORT(temperature,adresl,adresh);
			adc_started=0;
		}
		adcon0.GO_DONE=1;
		adc_started=1;
	}
}

void init_ADC(){
	adcon0 = 0;
	adcon1 = 0b1110; // AN0 is analog input, all others are digital, VSS and VDD as voltage references	
	
	adcon2.ADFM =1;   //right side adjustment
	adcon2.ADCS2=1; //conversion clock= 48/64
	adcon2.ADCS1=1;
	adcon2.ADCS0=0;
	
	adcon2.ACQT2=1;
	adcon2.ACQT1=0;
	adcon2.ACQT0=0; //wait sampling time 8tad +/-10µs?
	adcon0 = 1;     //enable A/D
}

bool is_int(unsigned char * str){
	if (*str=='-') *str++;
	if (*str==0) return false;
	while (*str>='0' && *str<='9') str++;
	return *str==0; //end of string no other characters
}

void main()
{
	//tacho_time_ptr=(unsigned char *) & tacho_time;
	//general configuration
	ucon.3=0; //turn off USB
	ucfg.3=1; //turn usb transceiver off	
	
	rcon.IPEN=1; //enable interrupt priority
	adcon1 = 0x0F; //initialize the AD con 1 to enable digital inputs
	ipr2.USBIP=0; //low priority for USB interrupts
	
	//analog
	init_ADC();
	
	//IO:
	TRIAC_OUTPUT=TRIAC_OFF;
	cmcon=7; //disable comparator	
	trisa.0=1; //analog input
	trisa.2=0; //output boost
	trisa.3=0; //output direction
	trisa.4=0; //triac
	trisa.5=0; //LED
	trisa.1=0; //test
	trisb.0=1; //INT for zero crossing
	TRIAC_OUTPUT=TRIAC_OFF;
	
	trisc.1=1; //CCP2 input
	trisc.2=1; //CCP1 input
	trisc.7=1; //RX
	trisc.6=0; //TX
	
	LED_OUTPUT=1;
	BOOST_OUTPUT=0;
	DIRECTION_OUTPUT=0;
	
	//init serial port
	serial_init();
	
	//configure edge detection for zero crossing, synchronizing the TMR2
	intcon2.INTEDG0=0; //falling edge
	intcon.INT0F=0;
	intcon.INT0E=1;
	
	//configure TMR2 used for determing when to turn on TRIAC
	t2con.T2CKPS0=1;
	t2con.T2CKPS1=1;
	t2con.TOUTPS0=0; // 1
	t2con.TOUTPS1=0;
	t2con.TOUTPS2=0;
	t2con.TOUTPS3=0;
	pr2=74; // 750kHz / 75 = 10KHz
	pie1.TMR2IE=1;
	t2con.TMR2ON=1;
	
	//configure TMR0 for "RTC"
	t0con.T0CS=0;
	t0con.PSA=0;
	t0con.T0PS0=0;
	t0con.T0PS1=0;
	t0con.T0PS2=0;
	t0con.T08BIT=0;
	intcon.TMR0IE=1;
	intcon2.TMR0IP=0;
	t0con.TMR0ON=1;
	
	//configure TMR1 1.5 MHz and capture module for tacho coil
	t1con.RD16=1;
	t1con.TMR1CS=0;
	t1con.T1CKPS0=1;
	t1con.T1CKPS1=1;
	t1con.TMR1ON=1;
	ipr1.TMR1IP=1;
	pie1.TMR1IE=1;
	
	ccp1con.CCP1M0=1; //capture every rising edge
	ccp1con.CCP1M1=0;
	ccp1con.CCP1M2=1;
	ccp1con.CCP1M3=0;
	pir1.CCP1IF=0;
	pie1.CCP1IE=1;
	
	//set T3 for capture the water level sensor frequency (22-24KHz)
	//T3 runs at 1.5MHz capturing 16 rising edges = value * 1/1500000/16
	t3con.TMR3CS=0;
	t3con.RD16=1;
	t3con.T3CCP1=1;
	t3con.T3CCP2=0;	
	t3con.T3CKPS0=1;
	t3con.T3CKPS1=1;
	t3con.TMR3ON=1;
	ipr2.TMR3IP=0;
	pie2.TMR3IE=1;
	
	ccp2con.CCP2M0=1; //capture every 16th rising edge
	ccp2con.CCP2M1=1;
	ccp2con.CCP2M2=1;
	ccp2con.CCP2M3=0;
	pir2.CCP2IF=0;
	pie2.CCP2IE=1;	
	
	intcon.GIE=1;
	intcon.PEIE=1;

	if (rcon.TO==0){
		serial_send_string_line("wad!");
	}else{
		serial_send_string_line("start");
	}
	
	unsigned int i=0;
	unsigned int p_clock=0;
	
	while (1){
		if (output_power==0){
			triac_on=255;
			next_triac_on=255;
			TRIAC_OUTPUT=TRIAC_OFF; //make sure output is off
		}
		
		if (p_clock > clock) {
			p_clock=0;
		}
		
		
		if ((clock-p_clock)>9){ //+/- each 100m
			adjust_power();
			read_temperature();
			
			if (i==10){
				LED_OUTPUT = ~ LED_OUTPUT;
				serial_send_string("{pwr:");
				serial_send_int(output_power);
				serial_send_string(",tacho:");
				serial_send_long(get_tacho_time());
				serial_send_string(",rpm:");
				serial_send_uint(get_rpm());
				serial_send_string(",temp:");
				serial_send_uint(temperature);
				serial_send_string(",spd:");
				serial_send_int(wanted_speed);
				serial_send_string(",water:");
				serial_send_uint(get_water_level());
				serial_send_string(",err:");
				serial_send_uint(error);
				serial_send_string("}\n");
				i=0;
				error=0;	
			}			

			p_clock=clock;	
			i++;
		}
		
		if (serial_cmd_received){
			if (strcmp(rx_buff, "B=1")==0){
				BOOST_OUTPUT=1;
				serial_send_string_line("OK");
			}else if (strcmp(rx_buff, "B=0")==0){
				BOOST_OUTPUT=0;
				serial_send_string_line("OK");
			}else if (strncmp(rx_buff, "P=",2)==0){
				if (is_int(&rx_buff[2])){
					speed_control_enabled=false;
					set_power(atoi(&rx_buff[2]));
					serial_send_string_line("OK");
				}
			}else if (strncmp(rx_buff, "S=",2)==0){
				if (is_int(&rx_buff[2])){
					speed_control_enabled=true;
					set_wanted_speed(atoi(&rx_buff[2]));
					serial_send_string_line("OK");
				}
			}
			rx_idx=0;
			serial_cmd_received=0;
		}
		
		clear_wdt();
	}

}

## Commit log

2020-09-22 Add BOM
    add BOM
2021-08-07 Improvements
    Improvements of constant values
    random washing delay
    add detection for temperature sensor problems, prevent overheating
